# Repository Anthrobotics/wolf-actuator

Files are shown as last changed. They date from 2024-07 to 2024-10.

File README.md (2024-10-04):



# wolf-actuator [V1.2]
# Description
The WOLF actuator is a high-torque 3D-printable planetary robotic actuator. The design is based on the Wolfrom PGT, and does not require a planet gear carrier or planet gear bearings. All planet gears are equally spaced, and provide a large contact area for both the sun gear and ring gears. All gears are replaceable for added modularity and easy maintenance. [Modular crossed-roller bearings](https://github.com/Anthrobotics/modular-bearing) on both ends of the actuator provide WOLF with improved load-bearing capabilities, and smoother motion. The actuator is fully-backdriveable, and is capable of compliant control and force sensing. WOLF can be manufactured using a number of methods, including FDM and SLS 3D printing, and CNC machining.



# Improvements from V1.1
- An optional new encoder housing compatible with AMS AS5047 and AS5048 evaluation boards, using push-fit mounting instead of 4x M2x6mm bolts.
- Improved outer rings for mounting much larger loads (supporting 40mm wide mounts)
- A sample mount for a 2020 aluminum extrusion has been added
- [New upper and lower rings for the modular bearing](https://github.com/Anthrobotics/modular-bearing/tree/master/CAD/stl) for added strength
- A sample mount for securing WOLF to common 1-ton shop cranes

**Note, that no major changes are required from the previous assembly and usage guide. All the same steps can be followed, unless you use the new encoder mount. If that is used, simply use ***3x M4x14mm countersunk bolts*** to secure both the motor and encoder housing to the backplate. 1x M4x12mm bolt can be used to secure the motor into place before affixing the encoder holder.**

# Specifications
The specs of the V1.2 WOLF actuator are as follows:
- (Theoretical) Continuous Torque: 80 Nm
- (Theoretical) Peak Torque: 120 Nm
- Tested Peak Torque: 90 Nm
- Reduction: 34:1
- Weight: 1.55 Kg
- Max Operating Current: 58 A
- Operating Voltage Range: 24 VDC - 52 VDC
- Diameter: 202.3 mm
- Height: 67 mm
- Encoder: AS5047P



# Testing
A number of tests have been performed on V1.1 and V1.2 of WOLF. The test model of WOLF was entirely 3D-printed using Polysonic PLA. Initial torque testing demonstrated that WOLF could output ~40.8 Nm of continuous torque, while consuming 10 A @ 30 VDC. Further testing will be performed to evaluate WOLF's performance at higher current limits, and with SLS-printed nylon gears. Peak torque achieved using PLA gearing (with no damage) is 90 Nm.

The actuator was capable of rotating the entire leg of our humanoid robot approximately 75 degrees in both forward and reverse directions. The weight of the leg is ~6 Kg, and 110 cm in height. 

Test video below (redirects to YouTube):

<div align="center">
      <a href="https://www.youtube.com/watch?v=Vza2nBm8GV0">
     Test Video
      </a>
    </div>

V1.3 testing is underway.

# Bill of Materials
You will need the following:

Printed components:
- 1x back plate
- 1x front plate
- 1x encoder magnet holder
- 1x encoder housing
- 2x internal ring gears
- 2x outer rings
- 12x planet gears
- 1x sun gear
- 2x [modular bearings](https://github.com/Anthrobotics/modular-bearing), WOLF actuator edition
- 1x planet gear alignment tool

**NOTE**: Some printable parts are labeled as *A* or *B*. Print one of each.

COTS components:
- 1x Eaglepower 8318 100KV brushless motor
- 1x AMS AS5047P (ABI/ABZ) encoder **OR** 1x AMS AS5048A (SPI) encoder
- 1x 6mmx2mm diametric encoder magnet (usually included with encoder)
- 27x M3x5mm heat-set inserts, brass (24x to mount actuator using front/back plates, and 3x to secure encoder housing)
- 12x M3x70mm bolts, socket head cap (to secure load)
- 12x M3x35mm bolts, socket head cap (to secure outer rings)
- 12x M3x0.5mm hex nuts, 2mm height (to secure outer rings)
- 3x M3x8mm bolts, countersunk (to secure encoder housing)
- 4x M2x6mm bolts, countersunk, self-tapping (to secure encoder into housing)
- 12x M3x0.5mm nylock nuts, 4mm height (to secure load)
- 4x M4x12mm bolts, countersunk (to secure motor to backplate)
- 4x M3x10mm bolts, countersunk (to secure sun gear to motor)

Tools:
- 3D printer
- Soldering iron w/ heat-set insert attachment
- Hex head drivers (M2, M3, M4)
- M3 wrench or compatible socket
- Tweezers (to assist with bearing assembly)
- PTFE lubricant (Super-Lube) for bearings and gears

# Assembly Guide
See the included V1.1 Assembly and Usage Guide PDF. (No major changes in V1.2, so the previous guide can be followed.)

# Usage
WOLF can be used in a number of applications, including:
- Humanoid robots
- Large quadruped robots
- 3-Axis motion systems
- Unmanned Ground Vehicles (UGV)

**WARNING: DO NOT place fingers or appendages near the gearing of the actuator while it is in motion.**

# Contribute

Contributions from the community are welcomed! Please send us a message if you are interested in collaborating.

# License

Shield: [][cc-by-sa]

This work is licensed under a
[Creative Commons Attribution-ShareAlike 4.0 International License][cc-by-sa].

[][cc-by-sa]

[cc-by-sa]: http://creativecommons.org/licenses/by-sa/4.0/
[cc-by-sa-image]: https://licensebuttons.net/l/by-sa/4.0/88x31.png
[cc-by-sa-shield]: https://img.shields.io/badge/License-CC%20BY--SA%204.0-lightgrey.svg

# Contact

If you have any questions or need support, please feel free to open an issue or contact us at:

Email: support@anthrobotics.ca

Website: [anthrobotics](https://anthrobotics.ca/)

Twitter: [@anthrobo](https://x.com/Anthrobo)

# Gallery











# Attribution

This design is inspired by from the RFX gearbox by Robin Fröjd.

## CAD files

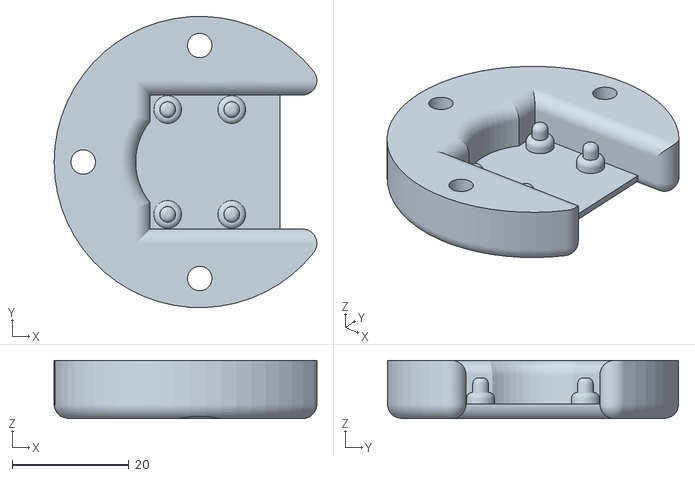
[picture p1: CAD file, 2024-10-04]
CAD/stl/encoder-housing-as5047.stl
45.1 x 50.0 x 10.0

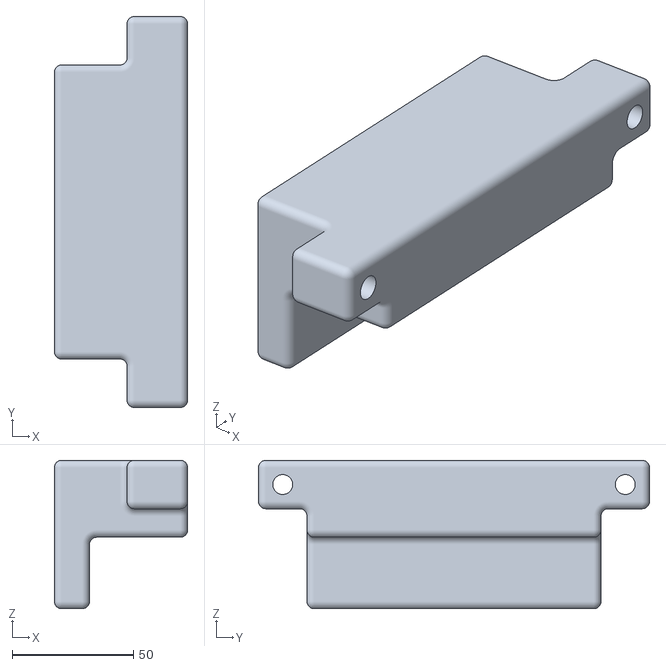
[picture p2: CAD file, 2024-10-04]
CAD/stl/shop-crane-bracket-B.stl
55.0 x 161.4 x 61.2

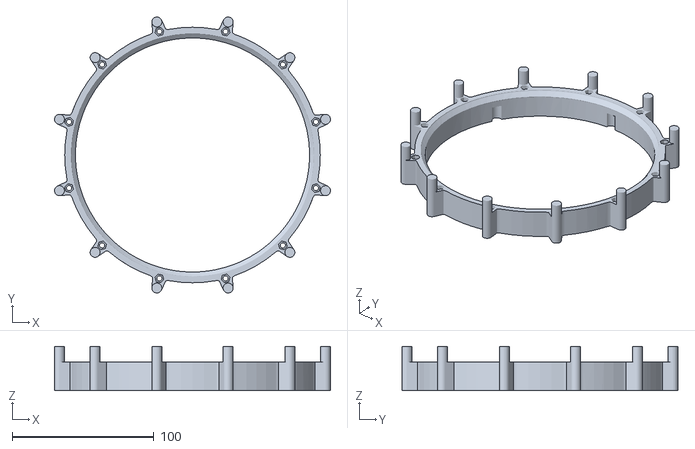
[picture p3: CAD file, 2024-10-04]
CAD/stl/outer-ring-B.stl
194.4 x 194.4 x 31.0

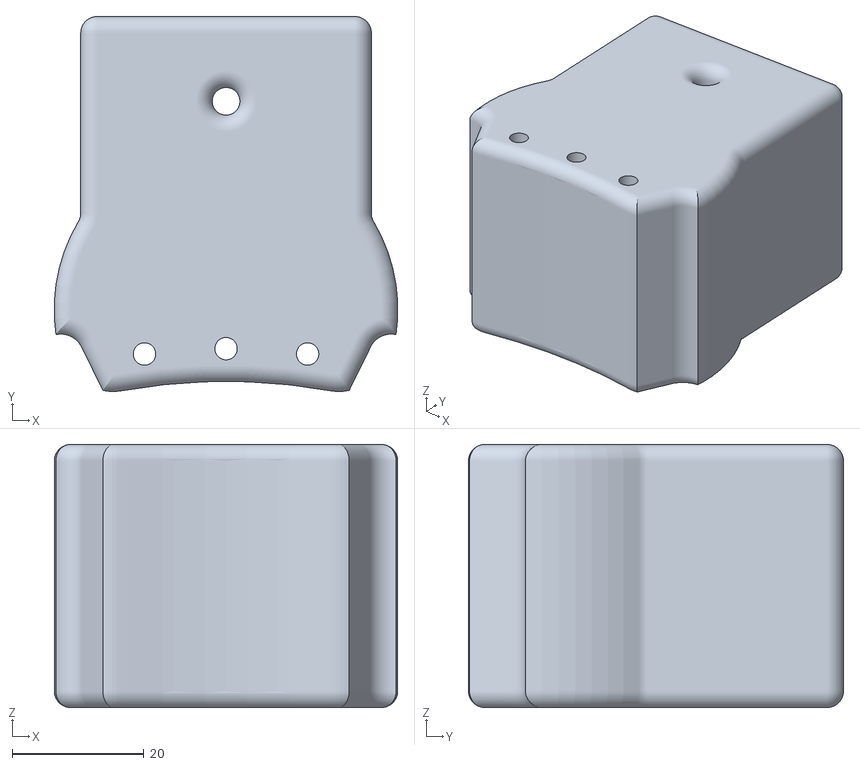
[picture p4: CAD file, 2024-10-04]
CAD/stl/load-arm-2020-ext.stl
52.2 x 57.0 x 40.0

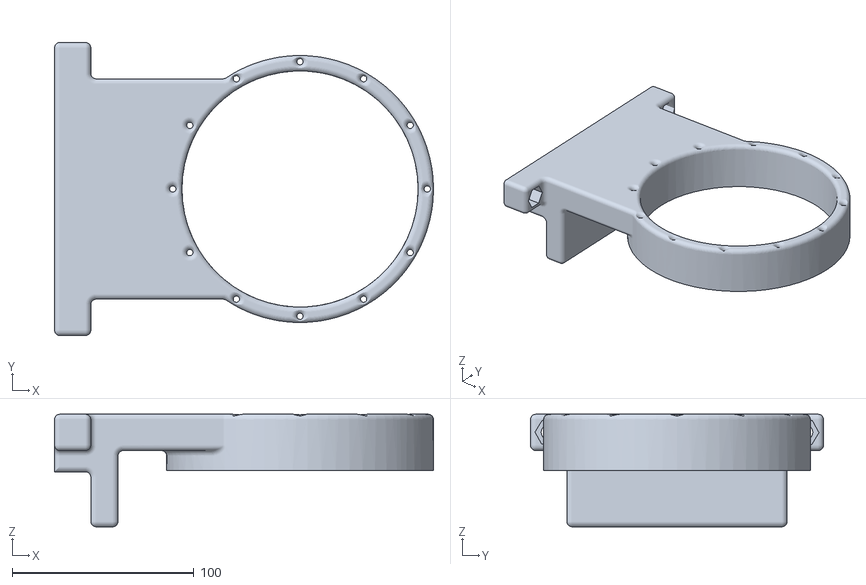
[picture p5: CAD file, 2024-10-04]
CAD/stl/shop-crane-bracket-A.stl
208.7 x 161.4 x 62.0

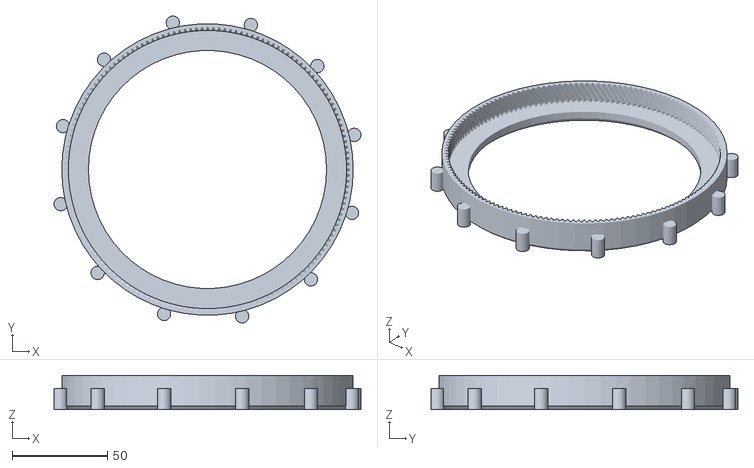
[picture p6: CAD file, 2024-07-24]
CAD/stl/front-plate.stl
161.2 x 161.1 x 18.0

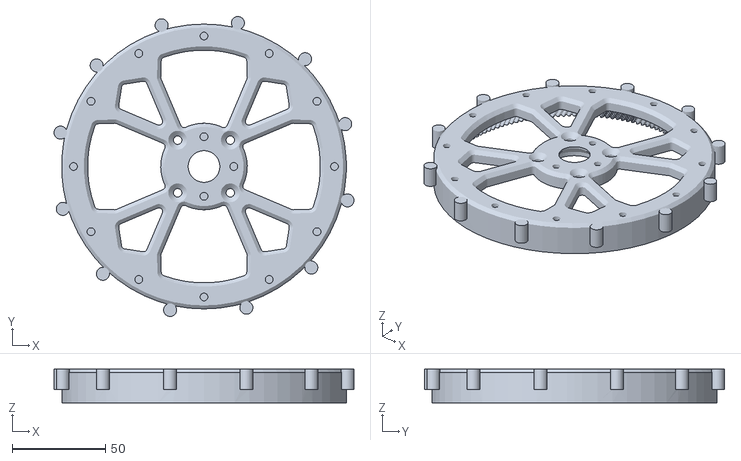
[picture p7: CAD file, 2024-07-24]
CAD/stl/back-plate.stl
161.1 x 161.2 x 18.0

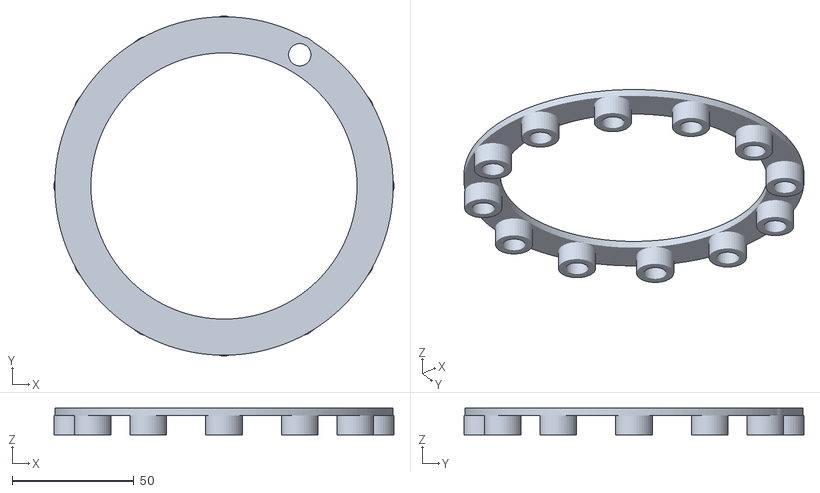
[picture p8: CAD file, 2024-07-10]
CAD/stl/planet-gear-alignment-tool.stl
139.9 x 139.9 x 11.0

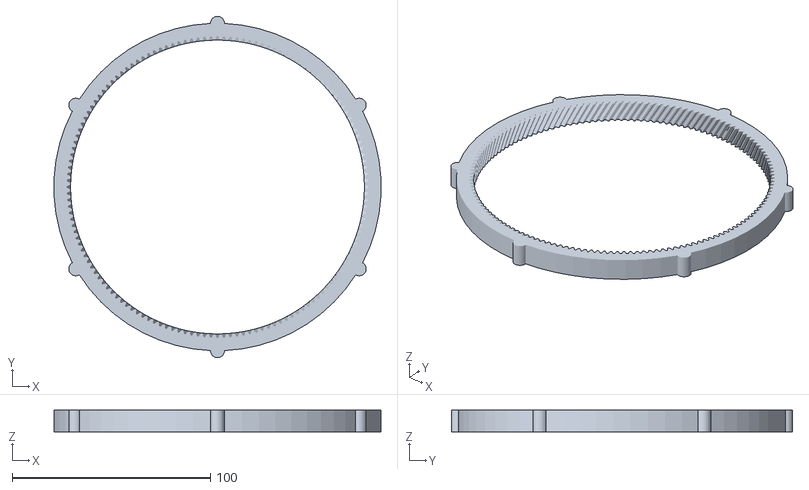
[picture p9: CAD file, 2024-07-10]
CAD/stl/internal-ring-gear-A.stl
164.8 x 172.0 x 11.0

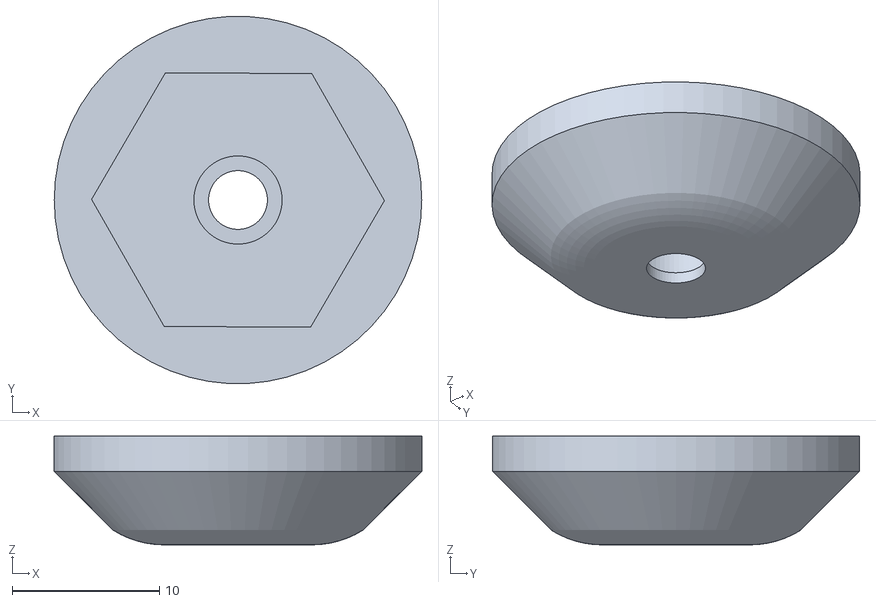
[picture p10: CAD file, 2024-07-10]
CAD/stl/encoder-magnet-holder.stl
25.0 x 25.0 x 7.40

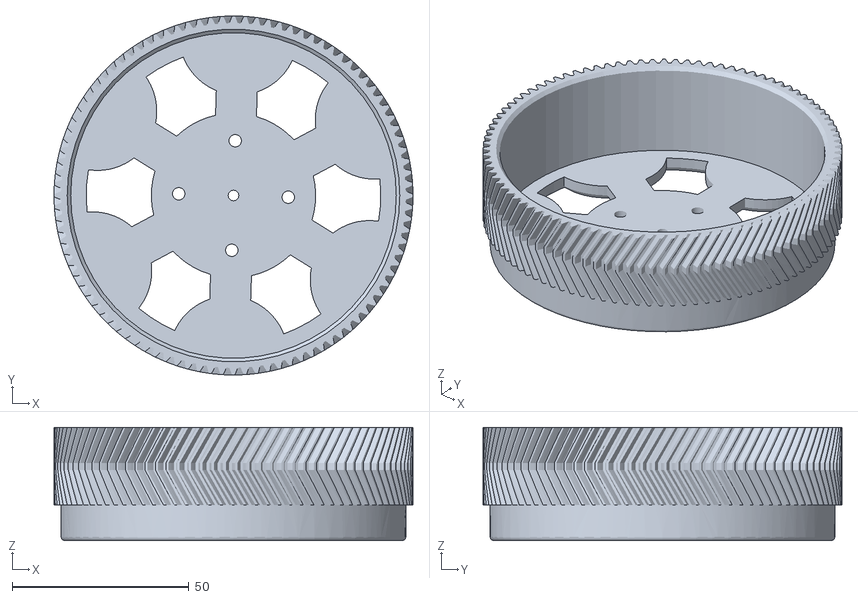
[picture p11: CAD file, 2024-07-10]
CAD/stl/sun-gear.stl
101.6 x 101.6 x 32.0

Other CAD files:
CAD/stl/outer-ring-A.stl
CAD/stl/planet-gears.stl
CAD/stl/internal-ring-gear-B.stl

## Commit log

2024-07-10 Uploaded v1 stl files
    [Roller.stl, back-plate.stl, encoder-housing.stl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]
2024-07-10 move file
    [roller.stl]
2024-07-10 fixed planet gear file
2024-07-10 Uploaded planet gear alignment tool
    [planet-gear-alignment-tool.stl]
2024-07-10 Update README.md
    Added Initial BOM
2024-07-12 Added roller-set stl file
    Will make it easier to print batches of 42x rollers.
    [roller-set.stl]
2024-07-15 Uploaded Assembly and Usage Guide
    V1.0, PDF copy
2024-07-24 V1.1 Update from V1.0 (#1)
    * Update README.md
    * Delete WOLF Actuator Assembly and Usage Guide [V1.0].pdf
    Pending replacement with V1.1
    * Update README.md
    * Added V1.1 Assembly and Usage Guide
    * Delete CAD/wolf-actuator-V1-STEP.step
    Removed in preparation for V1.1 STEP
    * Delete CAD/stl/back-plate.stl
    In preparation for V1.1 release
    * Delete CAD/stl/front-plate.stl
    In preparation for V1.1 release
    * Delete CAD/stl/outer-ring-A.stl
    In preparation for V1.1 release
    * Delete CAD/stl/outer-ring-B.stl
    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
    [back-plate.stl, front-plate.stl, outer-ring-A.stl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]
2024-07-30 Delete CAD/stl/encoder-housing.stl
    Replaced with an improved model (encoder-housing-as5047.stl)
    [encoder-housing.stl]
2024-07-30 Uploaded new encoder housing file
    Fixes from the previous version:
    - optimized for self-tapping screws (M2x6mm)
    - fits the AMS AS5047P encoder with 2 rows of header pins
    - better fit against the backplate with enough clearance for the encoder magnet
    [encoder-housing-as5047.stl]
2024-07-30 Update README.md
    made note of using self-tapping bolts to secure encoder into encoder housing
2024-07-31 Update README.md
    Updated specifications to reflect updated measured weight (1.55 Kg).
2024-10-04 Updated files for V1.2
    Changes:
    - The encoder housing now uses a push-fit for AMS AS5047 and AS5048 evaluation board encoders.
    - Outer rings now longer have that 12mm gap between both, rather, they allow for one large 40mm gap for beefier mounts.
    - A simple shop crane mount for common 1 ton shop cranes allows for the actuator to be secured.
    - A sample mount for 2020 aluminum extrusion load arms has been added.
    [encoder-housing-as5047.stl, load-arm-2020-ext.stl, outer-ring-A.stl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]
